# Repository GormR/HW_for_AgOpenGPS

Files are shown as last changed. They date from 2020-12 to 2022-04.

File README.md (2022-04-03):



### What is "AgOpenGPS"?
AgOpenGPS "AOG" is an open-source project initiated by the Canadian [Brian Tischler](https://www.astech.ca/archives/indexofpastwinners/tischler-brian). It started as parallel driving aid and mapping software for Windows(TM) and turned into a full-control system for steering including section and rate control. Today, many peaceful people from all over the world collaborate and contribute to the project. 

The communication part of the software is called AgIO, and AgDiag is the software part showing an overview about all values exchanged between software and hardware. 

On the hardware side, there are several different solutions for the same job, beginning from just plugging readily available module together to the hardware designs provided in this repo for professional prototyping production, which supports all functions of AgOpenGPS in a dedicated design. 

All code is published under the [GNU general public license V3.0](https://www.gnu.org/licenses/gpl-3.0.html) on [Github](https://github.com/farmerbriantee/AgOpenGPS).


All hardware in this repository is published under the [Cern-OpenHardwareLicense-S-2.0](https://cern-ohl.web.cern.ch/).

This text is published under the non-commercial share-alike [Creative Commons License V4](https://creativecommons.org/licenses/by-nc-sa/4.0/deed.en).


All this keeps the project open for everyone in the future. Everyone is allowed to copy and produce everything of this project, but has to open her/his mods for the community in return.

This document describes the system and the hardware. A description of the software itself comes with [the manual embedded in the AgOpenGPS software packet.]([https://github.com/farmerbriantee/AgOpenGPS/releases)

Join the [AgOpenGPS forum](https://discourse.agopengps.com/) for further help and discussions.

>### Important Functional Safety Advice
>
>Agricultural steering systems have to meet at least the agricultural performance level AgrPL d acc. UN ECE R79 (see professional systems like [this](https://www.mobil-elektronik.com/uploads/media/Prospekt_Brochure_ME_Agricultural_Vehicles_ENG.pdf))!
>
>Especially with hydraulic control, the vehicle may likely get uncontrollable on a failure of the valve-controlling electronic which may result in fatal casualties or serious injuries!
>
>For AgOpenGPS, the required safety level may be archieved by the fail-safe absense of power for the valve/motor controlling unit, meaning this function must meet the requirements of AgrPL d.
>
>**Mind, that YOU are reliable for all what you do with this project!**

----
# Basic Block Diagram
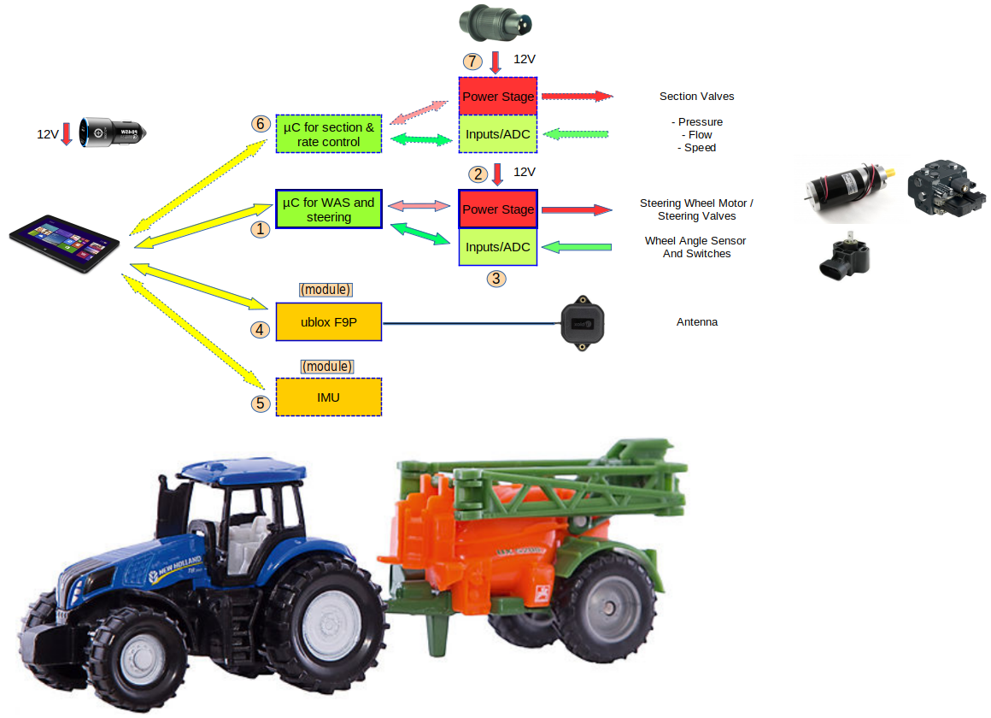
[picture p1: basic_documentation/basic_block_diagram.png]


1. µC e. g. Arduino Nano, Teensy4.1, ESP32,... controlling the power stage and sampling wheel angle sensor (WAS) and optionally IMU data. Also reads the switches 
2. Power stage to drive a motor or hydraulic valves
3. Input section: Analog-digital converter for WAS signal and decoupling for buttons
4. Satellite navigation receiver (GNSS) with RTK precision + antenna (one or two sets)
5. IMU unit
6. Section and rate control (option)
7. Power stage and analog frontend for section and rate control

All blocks but the antennas may be integrated into one PCB - see "Central Units"

# Getting Started, Level 1: Parallel Driving Aid and Mapping

A tablet/notebook/convertable computer running Windows and an RTK-enabled GNSS (GPS) receiver is needed. Read [the posts in the forum](https://discourse.agopengps.com/search?q=which%20tablet) to find a suitable tablet. The screen and its brightness is of highest importance. Other helpful features, you may need, are GSM (mobile data) for the reception of NTRIP data for real-time correction of the GNSS data (instead of using the mobile phone), easy charging for 12V or Ethernet, if USB is not used.

The "standard" RTK GNSS receiver for AgOpenGPS is based on the [ZED-F9P module from ublox](https://www.u-blox.com/en/product/zed-f9p-module), if you don't have an onboard receiver in the tractor. Ready-to-use boards ship from [Ardusimple](https://www.ardusimple.com/product/simplertk2b/) for less than 200€ or $. This is the only option where you can start with a single antenna and migrate to dual-antenna later one. Even two Ardusimple boards are by far less expensive than dual-receivers from [Serpentrio](https://www.septentrio.com) or [Bynav](https://www.bynav.com/). There is no noteworthy difference in precision between these receivers. The Ardusimple board is the de-facto standard for AgOpenGPS. [Here](https://www.optimalsystem.de/os/docs/u-blox-gnss-konfigurationsanleitung.pdf) is a good introduction in German. For details of the technology see [J. M. Olivart i Llop, D. Moreno-Salinas and J. Sánchez: Full Real-Time Positioning and Attitude System Based on GNSS-RTK Technology](https://www.mdpi.com/2071-1050/12/23/9796/htm).

**Parts list**
- tablet/notebook/convertable computer for Windows 7 or higher
- [Ardusimple receiver with antenna](https://www.ardusimple.com/product/simplertk2b-basic-starter-kit-ip65/) or equivalent 
- USB-cable A-microB
- 12V charger for computer (optional but recommended)

**Installation:**
- Download and install [AgOpenGPS software packet]([https://github.com/farmerbriantee/AgOpenGPS/releases)
- Configure the Ardusimple with the help of the software ["ucenter"](https://www.u-blox.com/en/product/u-center) (not version 2!) and [this setup file](central_unit_2.0/code/Ardusimple_GGA_VTG_460.txt)
- connect charger - computer - GNSS-receiver - antenna in a row (the USB receptacle next to the antenna plug is the right one)
- start AgOpenGPS and configure the NTRIP server in AgIO
- put the antenna outside and see, if position data is received (should lock to RTK after a while)
- start mapping with AgOpenGPS

"NTRIP" is the data needed to make cm-precision to GNSS positioning. Precise satellite-based navigation systems do not only a time-of-flight measurement, but also a detecting of the signal phases. Therefore, your position is send to a server every 10 seconds, and you receive customized correction data once per second in return. This only works well, if the server is located quite close to you (<30 km). The availability of public NTRIP serves varies from country to country. There is also the option to run [your own server](https://discourse.agopengps.com/t/rtkbase-a-gui-for-your-own-gnss-base-station/2341/214?u=goronb). 

Generally, the precision is impressive, when considering that light needs 1 second for 300,000km, so it only takes 33 nanoseconds = 0.000000033 sec per centimeter and even the wavelength of the GPS is much higher (about 20 centimeters).

Data sent by the GNSS receiver follows the [NMEA standard](https://en.wikipedia.org/wiki/NMEA_0183). For AgOpenGPS, the number of sentences should be as low as needed, so only "GGA" for position and "VTG" for speed vector.

# Level 2: Steering
There are two possibilities for steering: Turning the wheel like the driver does or driving the hydraulic system directly. Fortunately the electrical part is about the same (two PWM signals) and only the actuator differs: Either a DC motor or a dedicated proportional valve. 
For AgOpenGPS, feedback from a wheel angle sensor "WAS" is always needed, although an incremental sensor at the DC motor would work as well. The best choice is measuring the signal of the build-in WAS, if there is one, but there are also lots of how-tos for adding an additional WAS.

There are 3 different approaches for driving a motor or valves:
- plugging together readily available boards (e. g. Arduino Nano with ADS1115, BNO085 and IBT-2/Cytron - plans are in the AgOpenGPS ZIP file)

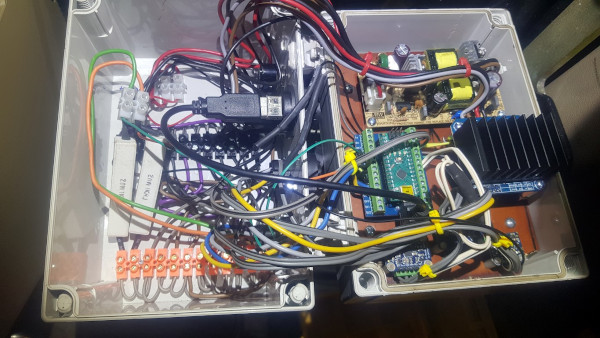
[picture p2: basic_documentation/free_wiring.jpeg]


- using a carrier board for those boards, which adds power supply and necessary components in classic "THT" technology (you have to solder all parts yourself - such boards are discussed in the forum)

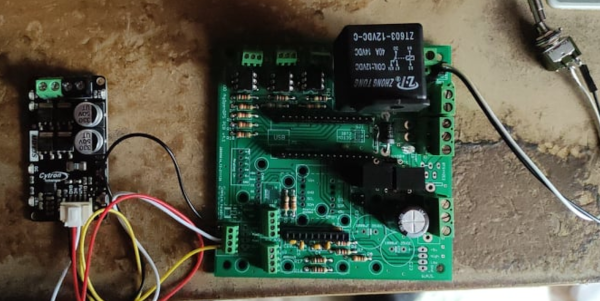
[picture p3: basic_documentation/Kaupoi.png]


- ordering one of the full-equipped board in this repository from a PCB manufacturer (only some "simple" parts have to be soldered by yourself)

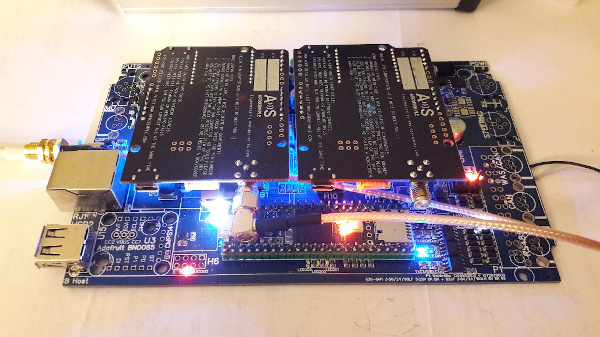
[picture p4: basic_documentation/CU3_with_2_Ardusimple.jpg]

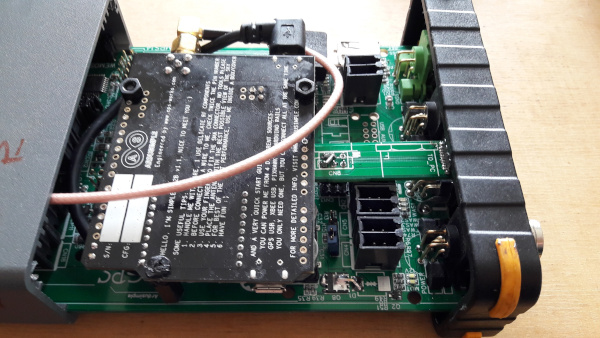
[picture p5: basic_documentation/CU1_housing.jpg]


Honestly, the last option is a nightmare these days, because some key parts (e. g. the automotive PWM power stage drivers) are not in stock from common distributors due to the general shortage in semiconductor industry these days (spring 2022). This means, you have to source from different suppliers and solder some SMD parts yourself, which is not easy in some cases. 

Nevertheless, this option is described in detail now:

**Parts list**
- tablet/notebook/convertable computer for Windows 7 or higher
- [one or two Ardusimple receiver with antenna](https://www.ardusimple.com/product/simplertk2b-basic-starter-kit-ip65/) or equivalent 
- IMU unit based on BNO08x
- mainboard + housing
- cables
- 12V charger for computer (the Central Unit 3.0 has a build-in charger, but no software support yet)
- steering wheel motor or hydraulic unit + support material

**Installation:**
- Download and install [AgOpenGPS software packet]([https://github.com/farmerbriantee/AgOpenGPS/releases)
- Configure the Ardusimple with the help of the software ["ucenter"](https://www.u-blox.com/en/product/u-center) (not version 2!) and [this setup file](central_unit_2.0/code/Ardusimple_GGA_VTG_460.txt)
- assemble board and put it into the housing
- prepare cables 
- connect everything
- start AgOpenGPS and configure the NTRIP server in AgIO
- put the antenna outside and see, if position data is received (should lock to RTK after a while)
- start working with AgOpenGPS

# Hints for Wiring
All signals to the motor or hydraulic valve shall be inside a single cable. This cable may only be connected to the Central Unit and the motor/valve unit - nowhere else. So no connection between the valve unit and the chassis as long as you don't want to use your equipment for short-wave broadcasting!

WAS:
If there is a dedicated WAS for AgOpenGPS, use a 3-pole calbe running from the Central Unit to the WAS. It contains the signals +5V, "WAS" = analog output of the WAS and 0V = GND. No other connections like "grounding" somewere in this case either! If a factory-assembled WAS shall be "sourced" like in the following pictures, a two-pole cable with the signals "WAS" (again the analog output of the WAS) and "WAS_N" is needed. Mind that the cable number differs! Connect "WAS_N" to 0V next to the point where you already connected the "WAS". 

The original wire was not cut but the isolation was just partially cut from one side. Advantage here: It's inside the cabin and always dry.

With one of the central units, select "differential" in AgOpenGPS in both cases.

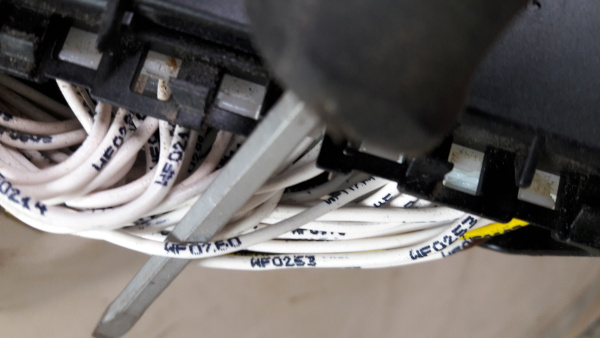
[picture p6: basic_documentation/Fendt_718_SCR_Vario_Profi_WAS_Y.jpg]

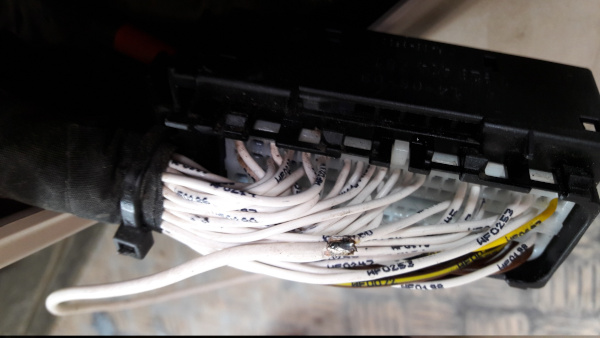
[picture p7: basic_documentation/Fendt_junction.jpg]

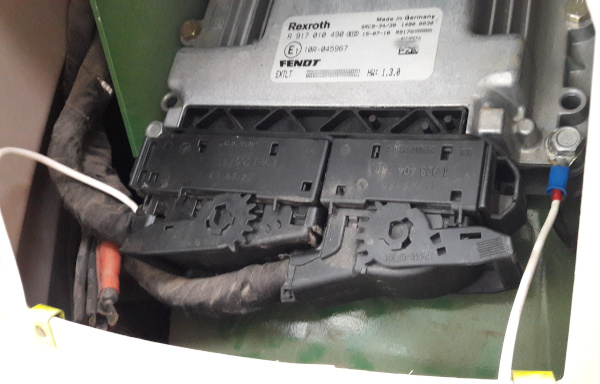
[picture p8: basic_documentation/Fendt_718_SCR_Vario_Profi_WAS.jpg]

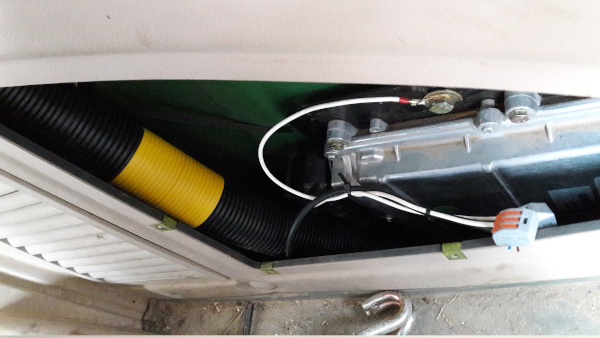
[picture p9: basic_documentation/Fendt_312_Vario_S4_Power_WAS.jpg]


There is intentionally no coupling of 0V from power stage and computer side on the Central Unit 1.x and 2.x, because the charger unit has that normally. If this is not the case (e. g. you're using an inverter and a charger with mains plug), the connection must be done manually.

# Dual-GNSS? IMU? Both?
When you living in a plain area with no hills, you can start farming now. But likely there are rolling hills around and your fields are sloping a little bit, so that the antenna position swings left and right with the slope of the field and there is a need to compensate that by either using two antennas with two RTK receivers or and an	inertial measurement unit (IMU). 

Pros of dual antenna are:
- always absolute position in the room
- antenna diversity: if one antenna does not receive the signal due to trees, the other one will take over for that time

Pros of IMU:
- Cheaper
- Roll angle is more exact
- Reduced update rate if using two Ardusimple with cross-communication (8Hz instead of 10Hz). Solution: Connect both F9P directly to the PC via USB (same setup file).
 
The z axis of the IMU must be exactly the vertical axis of the vehicle. Recommended is the use of an BNO085 or BNO080 - directly or embedded in the CMPS14 board.

# Arduino-Nano or Teensy-based?
For all 3 different approaches, these two options are available (plus ESP32 to name the third). The Teensy has more memory and is faster - both more than 100 times). The advantage today is: simply nothing, as long as you don't use CAN or main parts of AgOpenGPS run inside the iMX controller. Maybe in future, AgOpenGPS will migrate there and has just have a web page on any mobile device. This would also improve the steering behaviour noteworthy due to reduced jitter times (no Windows in between).

# IBT-2 or Cytron
First of all: None of them for driving a Danfoss block - a rail-to-rail operational amplifier will do that job as well.

Intergrated boards will always use what the IBT-2 is using, because there is no need to care for short-circuits due to miswiring or mechanical damage. The drivers have a build-in protected agains all that. And there is no need for a freewheeling relay if a steering wheel motor is used. 

When using complete boards, further arguments matter: Yes, the IBT-2 is cheaper, but there are a lot of bad-quality boards out in the wildlife. Control the solderings and always add a thermal pad between the board and the heat sink! The solder mask is no suitable isolation between the PCB and the heat sink! These qualitiy problems are avoided by buying the Cytron. But the Cytron blocks manual steering, when AgOpenGPS isn't in control, because it short the motor wires - it acts as electrical brake, which is not intended in this use-case. Any kind of disengagement is needed.

# USB or Ethernet
Many discussions have been made about the "right" interface between the computer and the peripherals. In fact: Both kind of connectors, USB and Ethernet, are not suitable for agricultural use. Professional systems use M8 and M12 connectors. The type "M12-D" is well-suitable for both Ethernet and USB, but no computer has such a connector... An option is soldering yourself, but another option is just having some spare cables in the box. 

An important point is the ability to transport supply power. For Ethernet, that makes some effort and only a few devices support PoE. USB always have that feature, so you can use just one USB-C cable for charging the computer and transfer data to the peripherals. Clear point of USB, as long as two-wire Ethernet is not commonly available for adequate costs.

My suggestion: If you ever dreamt of being a professional network admin, go for Ethernet. All others should use USB. Here, the Teensy may bring both worlds together by using RNDIS (Ethernet over USB) one day.

**Timing**

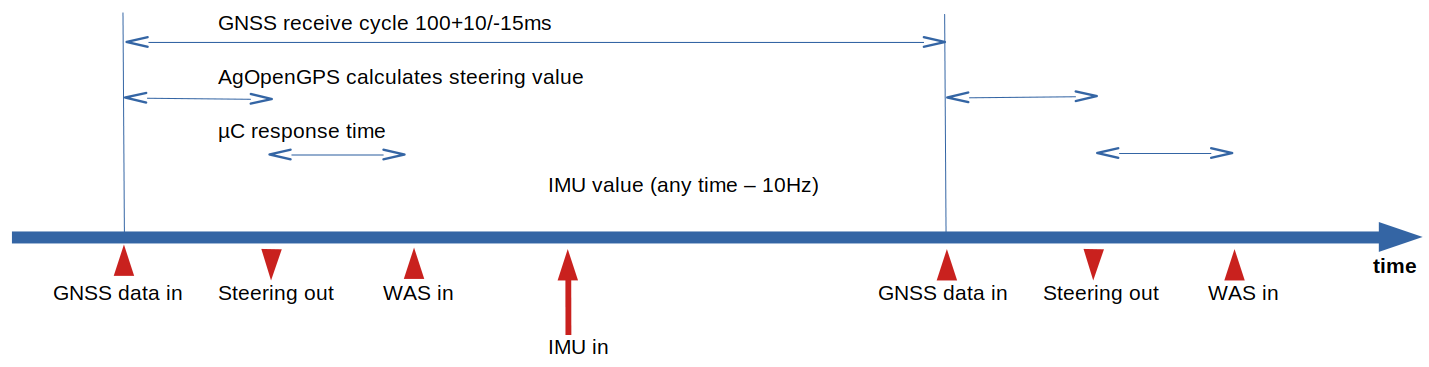
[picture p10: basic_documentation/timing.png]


This is the basic timing of AgOpenGPS. It is defined by the GNSS update cycle, so about 100ms for the F9P (Ardusimple) board. The postion data is an average of the last period, so the position is about 50ms "old". After having received that data, AgOpenGPS calulates all the steering data and sends it to the µC unit, that delivers the position of the steering (from wheel angle sensor) and optionally the IMU data in return. This is obviously not the best time, because that data is about 90ms old when processed by AgOpenGPS.

Using an extra µC for the IMU ("IMU_USB_v5_0.ino") even makes the timing even worse, because data receives at *any* time, so we don't have a delay but a fully unpredictable jitter. One workaround will come the AgOpenGPS V6 - there will be a unit that combines GNSS and IMU data into one non-standard NMEA sentence.

The best timing is archieved with no additional µC at all for GNSS and IMU. Both units are able to send serial data directly to the PC. All you need for the GNSS receivers is a USB cable and an USB-serial-converter cable for the IMU. The jitter simply can't be less.

Connection [of USB-Serial-Cable](https://de.aliexpress.com/item/32965292523.html) to BNO085 in RVC mode: 1st pic shows USB cable supplying board with 5V, if there is a voltage regulator on it; 2nd pic shows the same cable w/o using the voltage regulator. The 1st is prefered for this Adafruit board, the 2nd is for all boards w/o voltage regulator like shown in the 3rd picture. Supply voltage is about 3.05V in that case :+1:

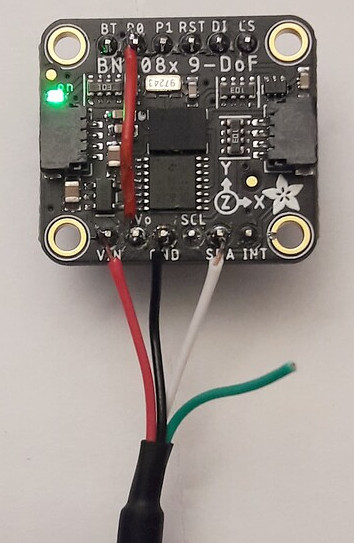
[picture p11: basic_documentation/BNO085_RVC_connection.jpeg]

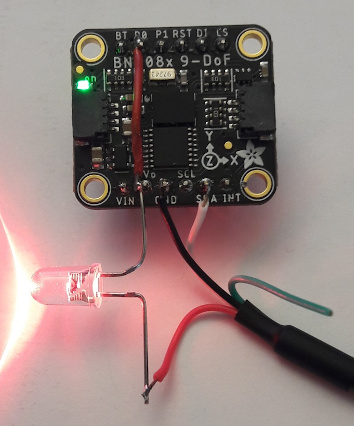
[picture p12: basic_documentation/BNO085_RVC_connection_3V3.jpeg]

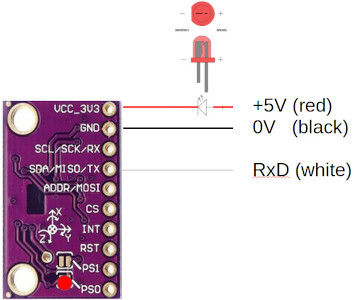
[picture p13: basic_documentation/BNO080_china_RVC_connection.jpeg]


For those who prefer Ethernet connections: This is how to connect two Ardusimple to AgIO via an Ethernet cable. [This module can connect two serial devices](https://www.pusr.com/products/dual-UART-to-ethernet-module-usr-tcp232-e2.html), in this case two [Ardusimples @ 460800Bd](https://github.com/GormR/HW_for_AgOpenGPS/tree/main/central_unit_2.0/code) to Windows. 

Will also work for one Ardusimple and one BNO085 in RVC mode.

The red wire is the +5V supply - FIVE volt supply.

black: 0V
red: 5V
brown: 3.3V
green: to Ardusimple (NTRIP; RxD@AS, TxD@USR)
white: from Ardusimple (NMEA data; TxD@AS, RxD@USR)

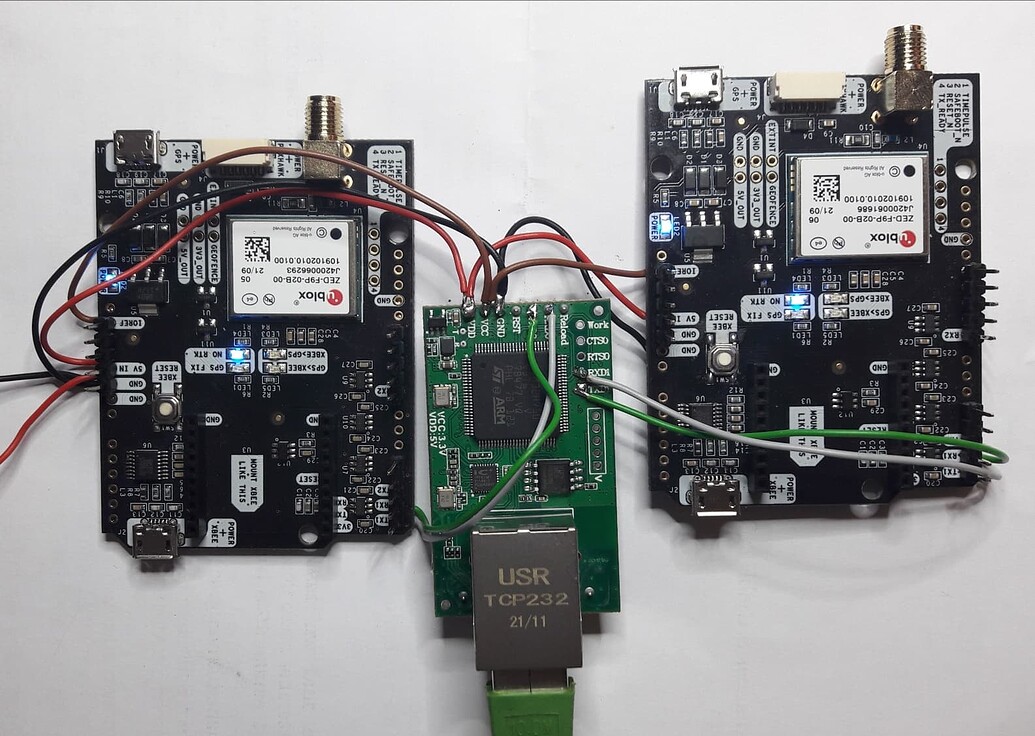
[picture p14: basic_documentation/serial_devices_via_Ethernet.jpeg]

(same colors used as above for the BNO085)

The connection to the Ardusimple board can also be made by [the plugable Pixhawk connectors using 0V, 5V and the two communication lines.](https://www.ardusimple.com/simplertk2b-hookup-guide/) In that case, connecting the 3.3V line is not needed, but I would put a 100 Ohms resistor in series with the com lines.

The BNO085 is difficult to buy these days, so it’s worth having a look at the Arduino Nano RP2040 Connect board with its integrated IMU. A prototype implementation using this one for AgOpenGPS can be found in [this Github repo](https://github.com/GormR/HW_for_AgOpenGPS/central_unit_2.0/code/Arduino_nano_connect_as_IMU/). The IMU itself is as good the the Bosch sensor of the BNO, but there is no magnetic sensor and so a continuous calibration of the heading isn’t possible so far. A certain drift is remaining, but may be eliminated in combination with AgIO one day.

With the Python script, the sensor emulated an BNO085 in RVC mode being compatible with the AgIO mod. [Here](central_unit_2.0/code/) is the replacement for the standard AgIO.exe. Just replace it by this file and work with the data of the BNO or Arduino Connect directly.

----
# Projects within the repository

All projects use a robust housing and industrial M12/M8 connetors (optional) as far as possible. There is also an option to use industrial PushIn connectors instead.

The PCB project was set up with the EDA program „EasyEDA“, which is freely usable. 

*These products are still working perfectly with AgOpenGPS, but not recommended for new systems*

[Documentation Central Unit](central_unit/README.md)

[Documentation Rooftop Unit](rooftop_unit/README.md)

[Documentation Ethernet Adapter for UDP](ethernet_adapter/README.md)

**Latest Main boards**

Update of Central Unit 1.x with 2nd slot for dual-Ardusimple:
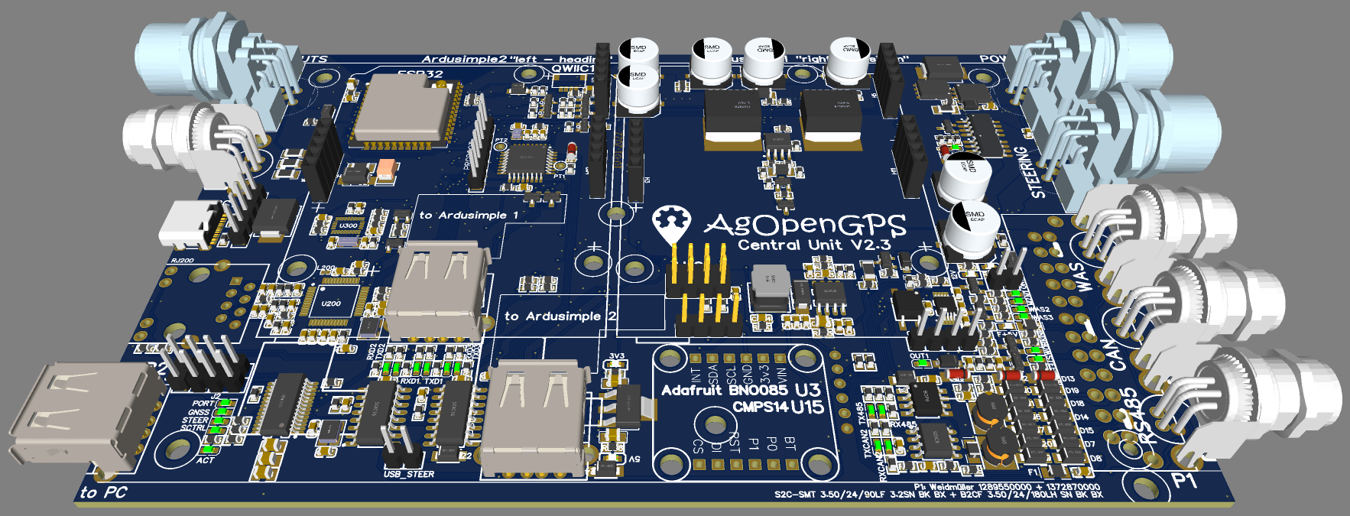
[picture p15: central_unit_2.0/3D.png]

[Documentation Central Unit 2.x](central_unit_2.0/README.md)

There is a [reduced BOM](central_unit_2.0/production_data/BOM_CentralUnit2.3_(USB-recommended).csv) for USB (estimated board price @ JLCPCB: $30 after the semiconductor prices will have returned to normal levels again).

Teensy-based central unit with additonal support for USB-PD hardware (no firmware support yet):
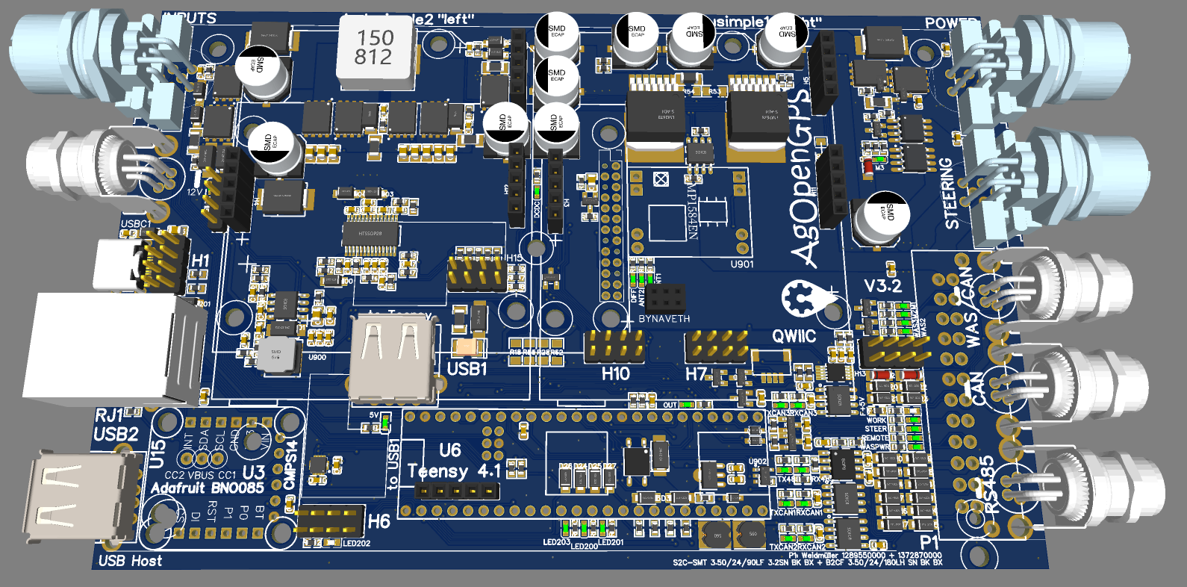
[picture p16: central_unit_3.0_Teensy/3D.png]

[Documentation Central Unit 3.x](central_unit_3.0_Teensy/README.md)

(This board also has a slot for Bynav-GNSS-receivers)

# Order How-To JLCPCB
- browse to [JLCPCB](https://jlcpcb.com) and click "Quote now"
- upload Gerber file (either for [Centrol unit](central_unit/production_data/Gerber_Central_Unit_AgOpenGPS.zip) or [Rooftop Unit](rooftop_unit/production_data/Gerber_Rooftop_Unit_AgOpenGPS.zip)). The Gerber of the central unit is too big for a preview, so you also have to enter the DIMENSIONS in the next line after the upload process has fully finished: 150 x 92mm²
- enter the number of PCBs to order: 5, 10, 15, etc
- if you like, you may change the color of the solder mask printing. But not all colors are available for SMD manufacturing!
- for the central unit check switch "SMT assembly" and "Assemble top layer"
- Accept terms and click "NEXT" (you may log in now)
- Upload [BOM](central_unit/production_data/BOM_Central%20Unit%20for%20AgOpenGPS.csv) and [Pick and Place file](central_unit/production_data/PickAndPlace_Central_Unit_AgOpenGPS.csv)
- click NEXT
- browse through the list and see, what is not confirmed. For some you may find 2nd sources, some maybe not available from stock in that moment, some like the Nexperia controller are unavailable and some like connectors are not supported yet (see my [video](https://www.youtube.com/watch?v=dLczChhmDCY) how to solder the USB-C receptacle; soldering the USB-C receptacle like this is only necessary, if you want to use a single USB cable for charging and data. USB itself is also connectable via a dedicated PushIn connector)
- click NEXT
- check if all components are placed correctly (e. g. rotation information is sometimes incorrect in the libraries)
- order

# (German copy)



### Was ist "AgOpenGPS"?
AgOpenGPS "AOG" ist ein open-source-Project, das vom kandischen Farmer [Brian Tischler](https://www.astech.ca/archives/indexofpastwinners/tischler-brian) initiiert wurde. Es war zunächst eine reine Parallelfahrhilfe und wurde nach und nach mit Hilfe der Community zu einem Lenksystem mit Teilbreitensteuerung. Die Software läuft nur unter Windows(TM) - es wird also ein Windows-Tablet oder Notebook benötigt. Inzwischen arbeiten Interessierte aus aller Welt friedlich an der Weiterentwicklung des Projektes. 

Die Software ist ein Set aus drei Programmen: Der Kommunikationsteil heißt AgIO, und AgDiag ist eine Anzeige aller Zustände und ausgetauschten Daten. 

Hardwareseitig gibt es vielfältige Ansätze für dieselbe Aufgabe. Das reicht von Anleitungen, wie man Arduino-Module mit Sensor- und Aktorboards zusammensteckt über Trägerplatinen, auf die man diese Module auflötet bis hin zu den in diesem Repository hinterlegten Modulen, die man als Fertigplatine bei einen Leiterplattenbestücker in Auftrag geben kann und die alle Funktionen von AgOpenGPS in einer Einheit unterstützen.

Die gesamte Software ist unter der  [GNU general public license V3.0](https://www.gnu.org/licenses/gpl-3.0.html) auf [Github](https://github.com/farmerbriantee/AgOpenGPS) veröffentlicht.


Alle Hardwareprojekte in diesem Repository sind unter der [Cern-OpenHardwareLicense-S-2.0](https://cern-ohl.web.cern.ch/) veröffentlicht.

Diese Beschreibung steht unter der nichtkommerziellen [Creative Commons License V4](https://creativecommons.org/licenses/by-nc-sa/4.0/deed.de).


Dadurch wird sichergestellt, dass das Projekt jetzt und in Zukunft allen zugänglich ist und alle Weiterentwicklungen der Community wieder zu Gute kommen.

Dieses Dokument beschreibt das System und die Hardsware. Eine Softwarebeschreibung befindet sich in einem [PDF, das sich im ZIP zusammen mit der Software befindet.]([https://github.com/farmerbriantee/AgOpenGPS/releases)

Es gibt ein (englisches) [AgOpenGPS forum](https://discourse.agopengps.com/), wo viele Leute unterschiedlichste Anwendungsfälle diskutieren.

>### Wichtiger Hinweis zur Funktionalen Sicherheit
>
>Fest verbaute Lenksystem, die z. B. in die Hydraulik eingreifen, müssen den Agricultural performance level AgrPL d nach UN ECE R79 (siehe z. B. professionelle Systeme wie [dieses](https://www.mobil-elektronik.com/uploads/media/Prospekt_Brochure_ME_Agrarfahrzeuge_DEU.pdf)) erfüllen!
>
>Im Falle eines Ausfalls und dadurch ausgelösten Lenkbewegungen kann es zu tödlichen Unfällen oder schweren Verletzungen kommen!
>
>Mit AgOpenGPS kann der notwendige Sicherheitslevel durch die fehlersichere Abschaltung der elektrischen Leistung für die Lenkaktoren erfolgen. Diese Abschaltung muss mindestens diesen Sicherheitslevel erfüllen.
>
>Alle Daten diese Repositories stehen unter der CERN Open-Hardware-Lizenz 2.0. Jede Haftung für Personenschäden und Sachschäden auf Grund Fehlern der Beschreibung oder Fehlern der Leiterplatte oder Software wird ausgeschlossen! 
>
>**Du bist dafür verantwortlich, was du mit diesem Projekt machst!**

----
# Grundlegendes Blockdiagram


1. µC, also z. B. Arduino Nano, Teensy4.1, ESP32,... steuert die Leistungsendstufe und liest die Werte des Lenkwinkelsensors (LWS = WAS), der Schalter nd ggf. der IMU ein
2. Leistungsendstufe, um den Motor oder die Hydraulik zu bedienen
3. Eingänge: Analog-digital-Wandler für das LWS-Signal und Eingangsstufe für die Schalter
4. GPS-Empfänger (GNSS) mit RTK-Genauigkeit + Antenna (ein oder zwei Paare)
5. IMU-Einheit
6. Teilbreiten- und Volumensteuerung (optional)
7. Leistungsendstufe und Analogteil der Teilbreiten- und Volumensteuerung

Alle Blöcke bis auf die Antennen können sich in einem Gehäuse befinden, z. B. auf den Leiterplatten in diesem Repository

# Getting Started, Level 1: Parallelfahrhilfe und Dokumentation

Für den Einstieg wird ein Tablet, Notebook oder Convertable mit dem Betriebssytem Windows une ein RTK-fähiger GNSS-(GPS)-Empfänger benötigt. Eine Beratung zum Rechner gibt es [in diesen Posts im Forum](https://discourse.agopengps.com/search?q=which%20tablet). Das ist natürlich immer nur eine Momentaufnahme. Wichtig ist in jedem Fall eine hohe Bildschirmhelligkeit. Weitere wichtige Punkte sind neben der Gesamtperformance die Möglichkeit, mobile Daten zu empfangen (eingebautes GSM-Modem), falls kein Handy dafür verwendet werden soll, um die NTRIP-Daten für die Positionskorrektur zu empfangen, eine einfache Lademöglichkeit für 12V und Ethernet, falls man USB nicht verwenden möchte.

Die Mehrzahl der RTK-GNSS-Empfänger für AgOpenGPS basieren auf einem [ZED-F9P-Module von ublox](https://www.u-blox.com/en/product/zed-f9p-module), aber auch bereits vorhandene Systeme der Traktorhersteller können verwendet werden. Fertige Empfängerplatinen gibt es z. B. bei [Ardusimple](https://www.ardusimple.com/product/simplertk2b/) für weniger als 200€. Das ist auch die einzige Möglichkeit, zunächst mit einem Ein-Antennen-System zu starten und später auf zwei Antennen aufzurüsten. Dabei sind zwei Ardusimples + zwei Antennen immer noch deutlich günstiger als Dual-Receiver von  [Serpentrio](https://www.septentrio.com) oder [Bynav](https://www.bynav.com/). Nennenswerte Genauigkeitsunterschiede haben die Systeme nicht. Das  Ardusimple-Board ist deshalb nicht umsonst der de-facto-Standard bei AgOpenGPS. 

[Hier](https://www.optimalsystem.de/os/docs/u-blox-gnss-konfigurationsanleitung.pdf) gibt es eine guten Anleitung zur Konfiguration. Grundlagen zur RTK-Technologie finden sich in [J. M. Olivart i Llop, D. Moreno-Salinas and J. Sánchez: Full Real-Time Positioning and Attitude System Based on GNSS-RTK Technology](https://www.mdpi.com/2071-1050/12/23/9796/htm) ein englischer Sprache.

**Einkaufsliste**
- Tablet/Notebook/Convertable-Computer mit Windows 7 oder höher
- [Ardusimple-Empfänger mit Antenne](https://www.ardusimple.com/product/simplertk2b-basic-starter-kit-ip65/) oder vergleichbarer Empfänger 
- USB-Kable A-microB
- 12V-Ladegerät für den Computer (optional aber empfehlenswert)

**Installation:**
- [AgOpenGPS software packet]([https://github.com/farmerbriantee/AgOpenGPS/releases) downloaden und installieren 
- Ardusimple konfigurieren mit der Software ["ucenter"](https://www.u-blox.com/en/product/u-center) (nicht die Version 2 benutzen!) und [diesen Setup-Daten](central_unit_2.0/code/Ardusimple_GGA_VTG_460.txt)
- Ladegerät, Computer - GNSS-Empfänger und Antenne einer einer Reihe verbinden (die USB-Buchse neben dem Antennenstecker ist die richtige)
- AgOpenGPS starten und den NTRIP-Server in AgIO konfigurieren (in D sollten im Allgemeinen die Daten von Sapos verwendet werden)
- Antenne nach draußen stellen und warten, bis Positionsdaten angezeigt werden. Nach einer Zeit sollte auch "RKT" angezeigt werden.
- Aufs Feld fahren und loslegen

Mit "NTRIP" werden Korrekturdaten bezeichnet, die benötigt werden, um eine Genauigkeit im cm-Bereicht zu erreichen. Dazu muss der Empfänger nicht nur die Signallaufzeit zwischen den Satelliten und der Antenne messen, sondern auch die Phase des Empfangssignals. Die notwendigen Korrekturdaten liefert ein NTRIP-Server, der über eine Referenzantenne verfügt, dessen Position hochgenau bekannt ist und sich in der Nähe befinden muss (< 30km). Man kann einen solchen Server auch [selbst](https://discourse.agopengps.com/t/rtkbase-a-gui-for-your-own-gnss-base-station/2341/214?u=goronb) betreiben, allerdings gibt es im deutschsprachigen Raum kostengünstige, professionelle Angebote wie z. B. SAPOS speziell for Landwirtschaft und Vermessung.

Folgende Daten werden für SAPOS benötigt:
- Server-IP (hier am Beispiel Nordrhein-Westfalen: www.sapos-nw-ntrip.de (AgIO kann damit automatisch die IP (hier: 80.158.61.104) und den Port (hier: 2101) ermitteln
- Benutzerkennung in der Form "nw-123456"
- Passwort in der Form "abcdef"

Insgesamt ist die erreichbare Genauigkeit beeindruckend, wenn man bedenkt, dass Licht und damit auch Funkwellen 300.000km in einer Sekunde zurücklegen, man also nur 33 Nanosekunden für einen cm benötigt und selbst die Wellenlänge der Trägerfrequenz mit ungefähr 20cm deutlich größer ist.

Ein GNSS-Empfänger sendet die Daten im [NMEA-Format](https://de.wikipedia.org/wiki/NMEA_0183). Die Einstellungen sollten so sein, dass möglichst nur die notwendigen Sätze "GGA" für Position und "VTG" für den Geschwindigkeitsvektor gesendet werden (s. u.).

# Level 2: Automatische Steuerung
Es gibt zwei grundsätzlich verschiedene Möglichkeiten der Steuerung: Direkt über Hydraulikventile oder mit Hilfe eines Elektromotors am Lenkrad drehen. Einen Eingriff in die Hydraulik sollten nur diejenigen vornehmen, die wirklich verstanden haben, was AgPL d bedeutet und es umsetzen können. Auch wenn es natürlich das eleganteste ist... Zu unterscheiden sind hier Systeme, die aus zwei Ventilgruppen bestehen (Steuerventil und Umschaltventil zwischen Lenkrad und AgOpenGPS-Steuerventil) und "intelligenten" Ventilinseln, wie z. B. "Danfoss".

Bei Lenkradmotoren hat sich der Phidgets-Motor als meistverwendeter herausgestellt, obwohl natürlich auch vergleichbare Motoren funktionieren. Zu unterscheiden sind Ankopplungen über ein Reibrad und Zahnradlösungen, bei denen das Ritzel des Motors in ein Zahnrad eingreift, das am Lenkrad festgeschraubt ist. Beide Lösungen haben sicherlich ihre Vorteile - wichtig ist, dass der Fahrer jederzeit ins Lenkgeschehen eingreifen kann! 

Motor oder Hydraulik: Zum Glück sind die Ansteuersignale dieselben: 2 PWM-Leistungssignale. Für das Umschaltventil muss bei Hydraulik zusätzlich noch ein Enable-Signal entsprechender Leistung bereitgestellt werden. "Danfoss"-Ventile können ebenfalls über 2 PWM angesteuert werden, es reicht allerdings ein einfacher Operationsverstärker als "Leistungsendstufe".

AgOpenGPS benötigt immer einen Lenkwinkelsensor, obwohl technisch auch eine Regelung über einen Tachogeber am Motor möglich wäre. Aber zum Glück haben ja viele Traktoren bereits eingebaute Sensoren, und es gibt auch sehr gute Anleitungen, einen Sensor einzubauen.

Für die Steuerung gibt es nun drei verschiedene Ansätze:
- man kauft sich fertige Teilmodule (Arduino Nano, ADS1115, ...) und verdrahtet diese "fliegend" in einem geeigneten Gehäuse



- man lässt sich eine fertige Leiterplatte herstellen, die für ein paar Euro aus China angeflogen kommt. Die Bestückung mit "klassischen" THT-Bauteilen muss man dann selber durchführen und auch die o. g. Teilmodule hier wieder auflöten



- man bestellt sich eine der vollständig bestückten Leiterplatten aus diesem Repository. Dann müssen nur noch die gewünschten Stecker angelötet werden.




In jedem Fall muss natürlich die Software auf den µC aufgespielt werden. Eine Beschreibung dazu befindet sich bei den einzelnen Leiterplatten.

Aus aktuellem Anlass muss aber leider gesagt werden, dass die letztgenannte Möglichkeit aktuell (Frühjahr 2022) sehr mühselig ist, da Schlüsselbauteile wie µC und Leistungstreiber nicht ab Lager verfügbar sind und somit anderweitig beschafft und selbst aufgelötet werden müssen. Leider kein Spaß für viele und erst einmal keine Besserung in Sicht.

**Einkaufsliste**
- Tablet/Notebook/Convertable-Computer für Windows 7 oder höher
- [ein oder zwei Ardusimple-Empfänger mit Antenne](https://www.ardusimple.com/product/simplertk2b-basic-starter-kit-ip65/) oder vergleichbarer Empfänger
- IMU auf Basis eines BNO080 oder BNO085 (auch als CMPS14-Board möglich)
- eines der Mainboard aus dem Repository hier + Gehäuse
- Kabel
- ein 12V-Ladegerät für den Computer (die Central Unit 3.0 hat ein eingebautes USB-C-PD Ladegerät, aber bisher keinen passenden Treiber)
- Lenkradmotor oder Hydraulikeinheit und Zubehör dafür

**Installation:**
- [AgOpenGPS software packet]([https://github.com/farmerbriantee/AgOpenGPS/releases) downloaden und installieren
- Ardusimple konfigurieren mit der Software ["ucenter"](https://www.u-blox.com/en/product/u-center) (nicht die Version 2 benutzen!) und [diesen Setup-Daten](central_unit_2.0/code/Ardusimple_GGA_VTG_460.txt)
- Mainboard mit Steckern bestücken und programmieren; Ardusimple-Boards aufstecken, wenn sie mit im Gehäuse sein sollen
- Kabel vorbereiten
- Alles verbinden
- AgOpenGPS starten und den NTRIP-Server in AgIO konfigurieren mit den eigenen Zugangsdaten (Sapos z. B.)
- Antenne im Freien aufstellen. Nach einer Zeit sollte der eigene Standort angezeigt werden und auch die Anzeige "RTK" erscheinen
- Los auf's Feld und AgOpenGPS ausprobieren

# Dual-GNSS? IMU? Oder beides?
Landwirte in im nördwestlichen Niedersachsen können jetzt loslegen. Alle anderen haben wahrscheinlich das ein oder andere Feld in Hanglage, und da läuft dann die eigene Position mit der Hangneigung weg, weil der Fußpunkt der Antenne zur Seite wandert. Also muss das kompensiert werden, wozu es eben diese beiden Möglichkeiten gibt: Eine zweite RTK-Empfänger/Antennenkombination oder eine IMU (inertial measurement unit - Inertiale Messeinheit, also ein Sensor, der die relative Lage im Raum an Hand der Schwerkraft und Massenträgheit bestimmen kann).

Vorteile Dual-GNSS:
- hat immer die absolute Position im Raum
- "Antenna-Diversity": Der kurzzeitige Ausfall einer Antenne führt nicht zum Verlust der Genauigkeit, z. B. wenn eine Seite von einem Baum abgeschattet wird

Vorteile IMU:
- Kostengünstiger
- Genauere Winkelerfassung
- Wenn zwei Ardusimple mit Querkommunikation betrieben werden (z. B. an einem ESP32), verringert sich die Datenrate der Position von 10 auf 8 pro Sekunde. Das kann aber umgangen werden, indem beide Boards direkt über USB mit dem PC verbunden werden (sie haben dann auch das gleiche Setup-File (s. o.).
 
Die z-Achse der IMU muss vertikal montiert sein. Es sollten BNO085 or BNO080-basierte Sensoren verwendet werden - allein oder als CMPS14-Board.

# Hinweise zur Verkabelung
Alle Signale, die zum Motor oder zur Ventilinsel führen, sollten in einem Kabel enthalten sein. Das Kabel darf nur an der Central Unit und am Motor oder an der Ventilinsel angeschlossen sein, sonst nirgendwo, also auch nicht die 0V an der Ventilinsel mit der Karosserie verbinden! Man baut sich so ganz schnell eine Rahmenantenne für Mittelwelle...

LWS/WAS:
Soll ein Extra-Lenkwinkelsensor verwendet werden, sollte ein 3pol. Kabel von der Central Unit zum Sensor verlegt werden, das die Signale +5V, "WAS" = Analogwert des LWS und 0V = GND enthält. Auch hier sollte nichts anderes angeschlossen sein, als der LWS, also auch wieder eine "Erdung" zur Karrosserie oder so. Wenn ein bereits verbauter LWS "angezapft" werden soll wie in den folgenden Bildern gezeigt, muss die Verdrahtung über ein zweipoliges Kabel "differenziell" erfolgen: "WAS" ist wieder der Analogwert des LWS, und "WAS_N" wird an einen 0V-Punkt in der Nähe des Punktes angeschlossen, wo auch "WAS" angeklemmt ist. Achtung: Die Klemmennummer variiert von Modell zu Modell - zumindestens bei Fendt. 

Im Bild wurde der Originaldraht nicht durchgeschnitten, sondern die Isolierung nur seitlich weggeschnitten, um den Draht für AgOpenGPS dann dort anzulöten. Zugentlastung nicht vergessen. Vorteil dieser Lösung: Es liegt alles im Trockenen in der Kabine.

Bei Verwendung der Central Units sollte in beiden Fällen in AgOpenGPS "differenziell" ausgewählt werden.






Bei der Central Unit 1.x und 2.x gibt es ganz bewusst keine harte Kopplung von 0V/GND der Leistungsendstufe und 0V/GND des USB, weil dies normalerweise über das 12V-Ladegerät erfolgt und eine Masseschleife vermieden werden soll. Sollte dies Verbindung nicht vorhanden sein, weil z. B. ein 230V-Netzteil an einem Wechselrichter betrieben wird, muss diese Verbindung manuell hergestellt werden.

# Arduino-Nano oder Teensy?
Für alle drei Möglichkeiten (Module zusammenlöten, auf Trägerplatine löten oder integriertes Board) gibt es zwei zur Auswahl stehende µC: der "klassische" Arduion-Nano-Controller ATMEGA368 oder das Teensy4.1-Board mit iMX1061-Controller von NXP. Der ESP32 und andere mal außen vor - sie haben ihre Daseinsbereichtigung z. B. für WLAN-Lösungen. Der Teensy ist mehr als 100x schneller, hat mehr als 100x mehr Speicher und hat somit - nein, bisher leider garkeinen Vorteil, solange AgOpenGPS weder CAN unterstützt oder wesentliche Softwareteile wirklich im iMX laufen und eine mobile Webside bereitstellen. Wäre super, weil sicherlich auch die Lenkqualität besser würde, ist aber noch Zukunftsmusik.

# IBT-2 oder Cytron
Vorweg: Für Danfoss reicht ein einfacher Operationsverstärker. Für alles andere muss schwereres Geschütz aufgefahren werden.

Die intergraten Board in diesem Repository werden immer die robusten, speziell für die Automobilindustrie entwickelten Infineon-Treiber verwenden, die auch auf dem IBT-2 verbaut sind, weil diese einfach vollständig gegen alle möglichen Fehler und Überlastung vollständig geschützt sind. Außerdem benötigt man nicht unbedingt einen Freilauf für das Lenkrad, weil der Motor nicht nennenswert elektromotorisch gebremst wird.

Wenn man eine Baugruppe fertig zukaufen möchte, kommen noch andere Argumente ins Spiel: Ja, ein IBT-2 ist günstiger, aber zumindeste die billigen China-Clones sind oft von wirklich lausiger Qualität. Hier muss man sich auf jeden Fall die Arbeit machen und den Kühlkörper abschrauben und mit Wärmeleitpaste oder besser einem Wärmeleitpad gegen die Leiterplatte isolieren. Der Lötstopplack alleine ist dafür vollkommen ungeeignet. Das hat zu einem schlechten Ruf dieser Lösung begetragen, ist aber - wie gesagt - auch leicht zu beheben.

Kauft man ein Cytron-Board, bekommt man immer gleich gute Qualität. Allerdings schließt ein Cytron die Motorwicklungen kurz, wenn AgOpenGPS nicht steuert. Dadurch ist es nicht mehr möglich das Lenkrad vernünftig leicht zu drehen. Ein Freilauf wird also auf jeden Fall benötigt.

# USB oder Ethernet
Unzählige Diskussionen gibt es, welches die beste Schnittstelle zwischen AgOpenGPS und der Hardware ist. Die ehrliche Antwort ist zunächst einmal: Sowohl USB als auch Ethernet haben für automobile/landwirtschaftliche Verwendung ungeeignete Stecker. Beide lassen sich allerdings mit den in professionellen Geräten verwendeten M12-D-Stecker versehen und sind dann sogar wasserfest bis IP67. Computer mit einem solchen Stecker sucht man allerdings vergeblich. Selbstlöten ist natürlich möglich oder nimmt Kabel von der Stange und legt sich ein paar als Ersatz ins Handschuhfach.

Ein wichtiger Punkt ist, dass der Anschluss auch den Versorgungsstrom liefern kann. Klarer Vorteil für USB - hier kann sogar der Computer während der Fahrt aufgeladen werden (Treiber vorausgesetzt - siehe oben). Der Vorteil mag sich zukünftig relativieren, wenn automobiles Zweidraht-Ethernet üblicher wird (Single-Pair Ethernet) und ICs zu vertretbaren Kosten für die AgOpenGPS-Gemeinde verfügbar werden.

Meine Meinung: Wer immer schon ein professioneller Netzwerk-Admin werden wollte, nimmt Ethernet. Alle anderen sind mit USB weit besser bedient, zumal man über USB auch das Netzwerkprotokoll fahren kann ("RNDIS").

**Timing**



Das Bild zeigt einen Zyklus von AgOpenGPS. Bestimmt wird das Timing vom Update-Zyklus des RTK-Empfängers, also ungefähr 100ms beim F9P, der auf dem Ardusimple-Board verbaut ist. Die gesendeten Positionsdaten sind also eine Mittelung über die letzten 100ms (ms = Millisekunden) und somit beim Empfang bereits 50ms "alt". Nachdem die Daten im Computer angekommen sind, berechnet AgOpenGPS die neuen Lenkvorgaben, sendet diese und bekommt als Antwort den Wert des Lenkwinkelsensors und die Daten der IMU, falls diese mit der Central Unit verbaut sind. Das ist ziemlich suboptimal, weil diese Daten dann schon mindestens 90ms alt sind, wenn AgOpenGPS mit den Positionsdaten verrechnet.

Also ein Arduino-Nano, Software drauf ("IMU_USB_v5_0.ino") und IMU dran. Leider nein, denn nun werden die Daten zwar alle 100ms gesendet, aber völlig asynchron zu den GNSS-Daten. Das wurde erkannt und "PANDA", ein proprieterer NMEA-Datensatz erschaffen, der GNSS-Daten und IMU-Daten zusammenfasst und an AgIO sendet.

Viel einfacher ist es allerdings, einen BNO080 oder BNO085 im "RVC"-Mode zu betreiben und direkt an den PC anzuschließen. Da ist nix dazwischen und daher die Lösung, die prinzipbedingt den geringsten Jitter aufweist. Dazu wird einfach ein [USB-TTL-Seriell-Kabel wie dieses](https://de.aliexpress.com/item/32965292523.html) an die IMU angelötet: Das erste Bild zeigt ein Board mit Spannungsregler, das mit 5V versorgt wird; das zweite Bild zeigt dasselbe Bord, aber mit Umgehung des Spannungsreglers - die Spannung beträgt dann 3.05V :+1:, und auf dem dritten Bild ist ein Board ohne integrierten Spannungsregler gezeigt. Ist ein Spannungsregler vorhanden, sollte die erste Lösung verwendet werden.





Für die Freunde des Ethernets: So kann man zwei two Ardusimple oder natürlich auch einen Ardusimple und die IMU mit AgIO über ein Ethernetkabel anschließen. Gezeigt ist hier [dieses Modul](https://www.pusr.com/products/dual-UART-to-ethernet-module-usr-tcp232-e2.html), hier mit zwei [Ardusimples @ 460800Bd](https://github.com/GormR/HW_for_AgOpenGPS/tree/main/central_unit_2.0/code). 

Der rote Draht ist der der +5V-Versorgung - in Worten: fünf Volt!

Schwarz: 0V
rot: 5V
braun: 3.3V
grün: zum Ardusimple (NTRIP; RxD@AS, TxD@USR)
weiss: vom Ardusimple (NMEA data; TxD@AS, RxD@USR)


(Es wurden dieselben Farben verwendet, wie beim Beispiel des BNO08x am USB-Kabel)

Alternativ zu einer Lötverbindung kann die Verbindung auch steckbar über die [Pixhawk Stecker unter Verwendung von 0V, 5V und den beiden RX- und TX-Drähten erfolgen.](https://www.ardusimple.com/simplertk2b-hookup-guide/) Eine Versorgung mit 3,3V ist in diesem Fall nicht notwendig, aber ich würde sicherheitshalber je einen 100Ohm-Widerstand in Serie zum Signal einlöten.

Leider ist der BNO085 egal in welcher Form derzeit schwer zu beschaffen, aber ein Arduino Nano RP2040 Connect-Board hat auch ein IMU und bietet sich so als Ersatz an. Eine prototypische Implementierung gibt für AgOpenGPS gibt es [hier in diesem Github Repo](https://github.com/GormR/HW_for_AgOpenGPS/central_unit_2.0/code/Arduino_nano_connect_as_IMU/). Die IMU selbst ist sicherlich nicht schlechter als die von Bosch des BNO085, aber da kein magnetischer Sensor mit verbaut ist, ist eine Nachführung des Headingdrifts nicht unmittelbar möglich. Mittelbar geht das sicherlich irgendwass einmal über AgIO, aber auch so ist die Drift ersten Versuchen nach sehr gering.

Mit dem hinterlegten Python(!)-Script simuliert das Board einen BNO085 im RVC-Mode. Dazu wird die erweiterte AgIO benötigt. [Hier](central_unit_2.0/code/) kann man die AgIO.exe mit direktem USB-Support für IMU und F9P/Ardusimple herunterladen. Einfach die Originaldatei damit ersetzen.

----
# Projekte in diesem Repository

Alle Projekte wurde in einem robusten Aluminiumgehäuse weitgehend mit industriellen M12/M8-Steckerverbindern realisiert. Es gibt aber auch die Möglichkeit, alternativ industrielle PushIn-Steckverbinder zu verwenden.

Alle Leiterplatten wurden mit dem kostenfreien Layoutprogramm „EasyEDA“ erstellt und lassen sich so direkt online bearbeiten. 

*Folgende Projekte funktionieren zwar ohne Einschränkung an AgOpenGPS, haben aber inzwischen verbesserte Nachfolger:*

[Dokumentation Central Unit](central_unit/README.md)

[Dokumentation Rooftop Unit](rooftop_unit/README.md)

[Dokumentation Ethernet Adapter for UDP](ethernet_adapter/README.md)

**Aktuelle Mainboards**

Update der Central Unit 1.x mit einem zweiten Steckplatz für dual-Ardusimple-Lösungen. Es kann auch nur eine Teilbestückung in Auftrag gegeben werden, bei der dann jeweils nur eine reine dual-Ardusimple-Einheit oder eine reine Motortreiber/Sensor-Einheit für zwei getrennte Gehäuse hergestellt wird.



[Documentation Central Unit 2.x](central_unit_2.0/README.md)

Es gibt eine [reduzierte Bauteilliste](central_unit_2.0/production_data/BOM_CentralUnit2.3_(USB-recommended).csv) für die meistverwendete USB-Variante, die für ca. 30€ herzustellen ist, wenn sich die Bauteilpreise denn mal wieder in normalen Höhen bewegen werden (Schätzpreis bei einer Bestellung von 5 Stück). 

Teensy-basierte Central Unit mit Unterstützung von USB-PD (Laden des Computers über USB-C; leider noch kein Firmware-Support bisher):

[Dokumentation Central Unit 3.x](central_unit_3.0_Teensy/README.md)

(Dieses Board hat auch einen Steckplatz für den alternativen Bynav-GNSS-Empfänger)

# Bestellhinweise
1. SMD-bestückte Leiterplatte bestellen, z. B. beim JLCPCB für ca. 35€ wie oben im englischen Teil beschrieben. Deutschsprachige Alternativen: PCB-Pool, Aisler. Vorsicht bei JLCPCB: Es werden nur die Bauteile bestückt, die zum Bestellzeitpunkt verfügbar sind (wird aber deutlich angezeigt - Liste kann auch heruntergeladen werden).
2. Je nach gewünschter Verkabelungsvariante entweder M8 + M12-Steckverbinder und Kabel bestellen oder PushIn-Buchsen und Stecker und ein passendes Gehäuse
3. Gewünschte Zusatzmodule bestellen, z. B. Lagesensor CMPS14 als (verbesserte) Alternative zum Onboard-Lagesensor MMA8452, zweiter RTK-Empfänger, ESP32 für CAN oder Dual-RTK, hier ebenfalls beschriebene Dacheinheit, RS232-Schnittstellenwandler, etc
4. Kleinkram wie Schrauben, (USB-) Kabel, Kunststoffabstandshülsen etc bestellen

Selbst gelötet werden die Steckverbinder wie unter 2. beschrieben (einfache zu löten). 

Weitere Hinweise finden sich zum Teil bei den einzelnen Baugruppen.

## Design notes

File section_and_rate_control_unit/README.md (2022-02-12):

# Section and Rate Control Unit for AgOpenGPS
(Informationen in deutscher Sprache unten)
Top view:
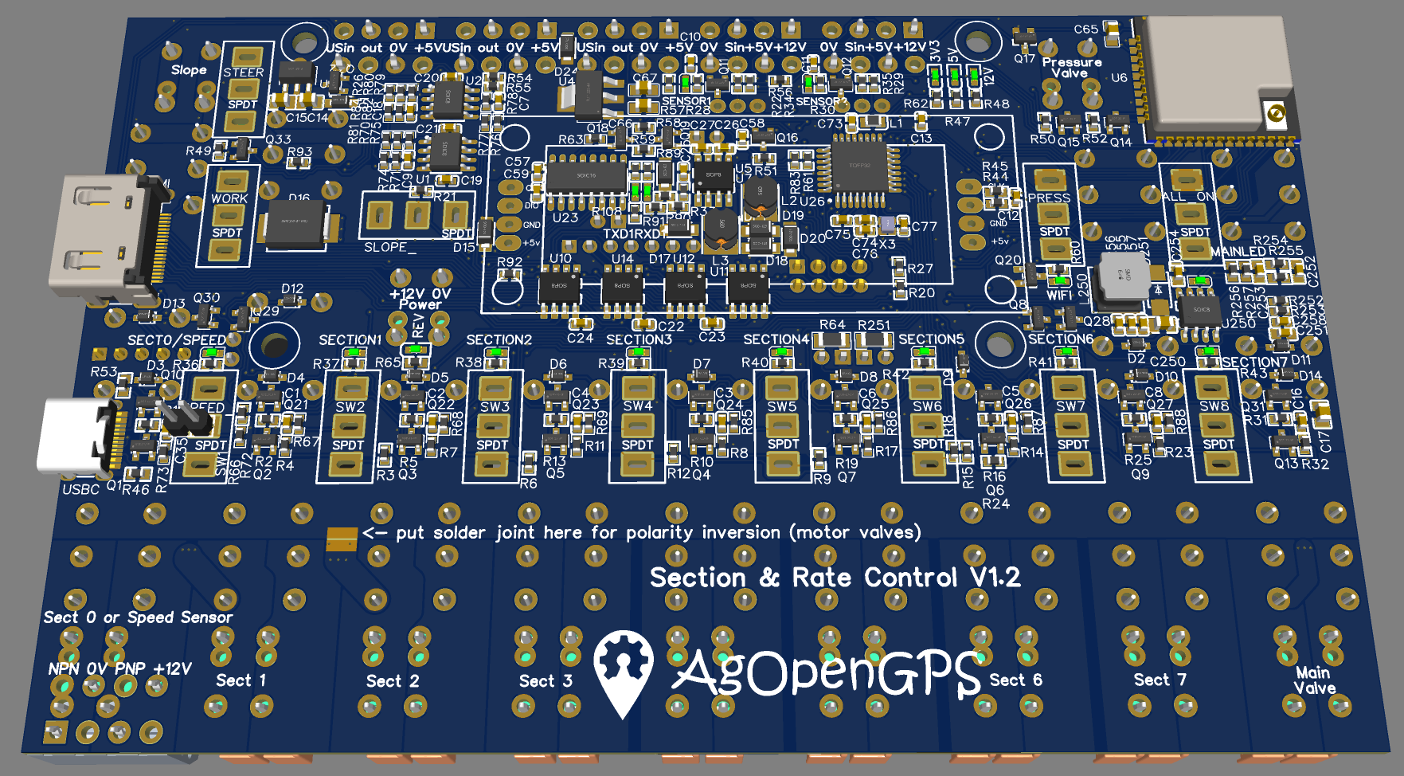
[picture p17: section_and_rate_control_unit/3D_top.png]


Bottom view:
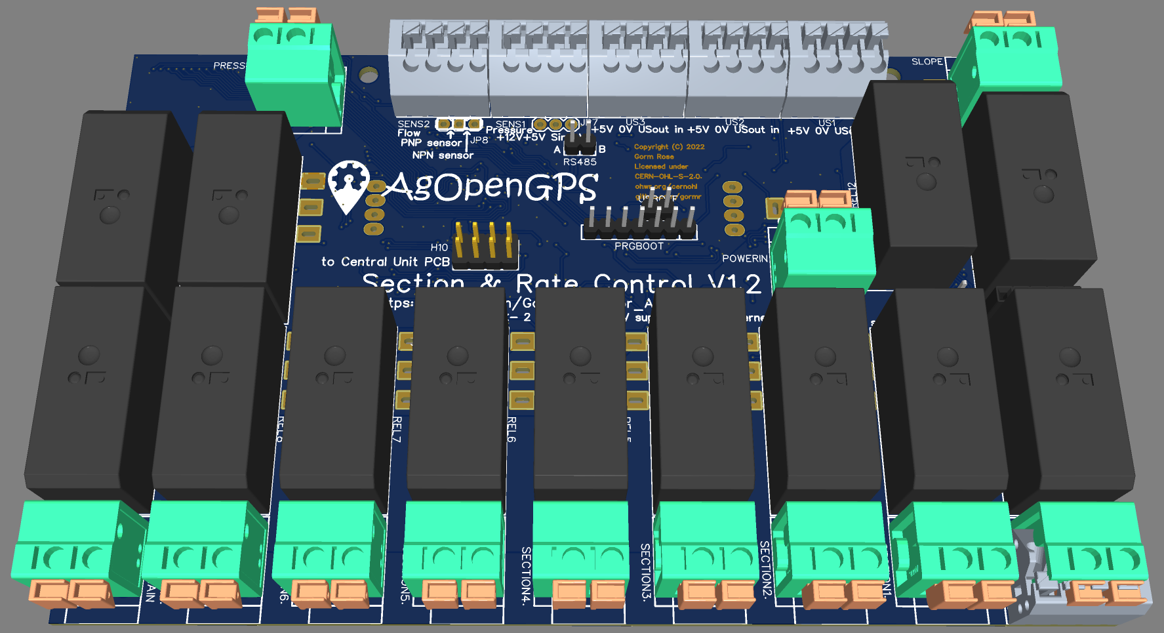
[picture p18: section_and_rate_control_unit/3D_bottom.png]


This project is a section control unit for AgOpenGPS. It is intended to be used together with the Central Unit 2.0 or Central Unit 3.0 (=Teensy) in the same or a separate housing (can be found here in Git as well). It may connected by either Ethernet, WiFi or RS485.

Brian's Concept only provided drivers for the sections w/o the possibility of manual interference. In that case, no rocker switches will be mounted, and the unit may also be located directly on the trailer.

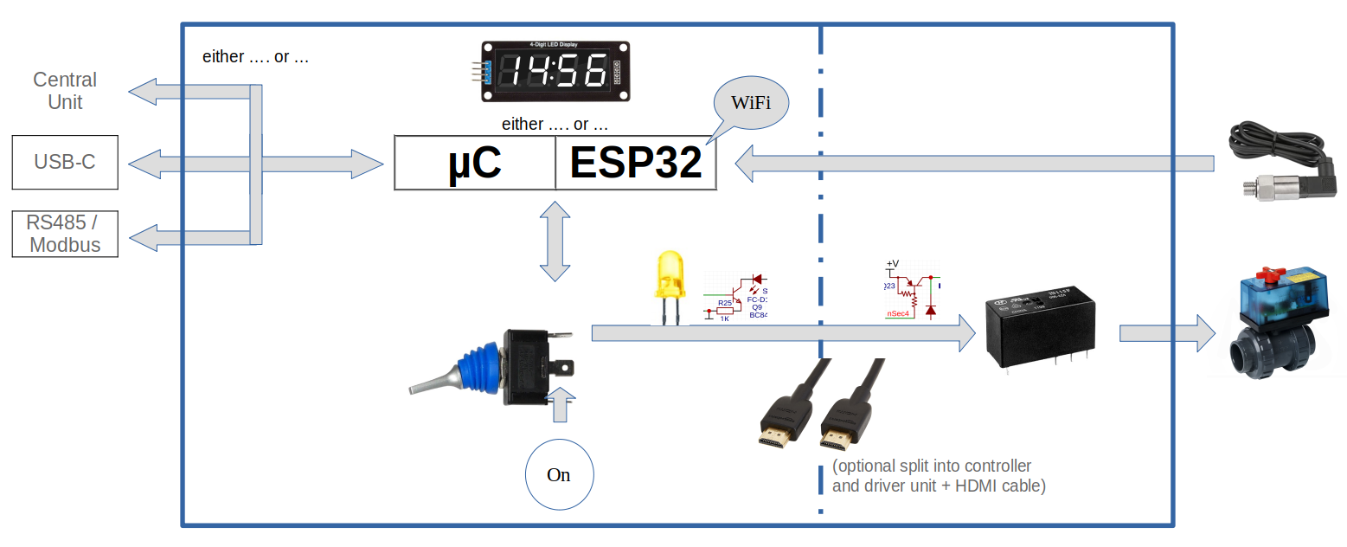
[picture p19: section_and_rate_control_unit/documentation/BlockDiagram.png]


MTZ8302 and WEder suggested a manual steering option in addition, so in general the functions provided by a Müller-Elektronik  control plus AgOpenGPS integration. To use that one or two of this PCB can be used, because both functions can either be provided on a single board or divided into two boards, of wich one contains the rocker switches and the µC and the other one (e. g. located on the trailer) the relays (and optionally another µC). If using a single µC-dual PCB solution, both units are conneced via a HDMI cable. If using two µC, options are USB, RS485, Ethernet or WiFi. 

Brian's software will work quite out-of-the box with minimal mods. MTZ8302's needs more adaptations, mainly due to the fact, that each pin can both drive the section and read back the status of the rocker switch.

- USB-C 
- Atmel section with I/Os needed for AOG
- connection to Ethernet via external module is possible
- power supply
- valves output
- RS485 / Modbus option
- ESP32 option (alternative to Atmel)

This setup does not include new functions but provides a robust, monolitic unit that may be manufactured by professionel EMS providers. 

Special focus is given to the robust housing and industrial PushIn connetors. 

# Detailed Description

In general, you can build up this unit as one (no need for the HDMI connector) or divide into a control unit that includes the µC and a power unit that might be directly on the trailer. On the power unit, you need all the parts from the schematic scheet "Machine Section Control" + parts around U3 (12V sensor supply if needed) only, and for the conrol unit on the other hand, you don't need that parts. The HDMI connector is needed on both PCBs for sure.

Heart of the section control is either an Atmel µC as U26 following [Brian's suggestion](https://github.com/farmerbriantee/AgOpenGPS/tree/master/Support/RateControl) or an ESP32 as U6 following [Matthias' suggestion](https://github.com/mtz8302/AOG_SectionControl_ESP32). For using grade control via ultrasonic sensors, the ESP32 is needed. If the ESP32 is used, X3 is not necessary and should be deleted from the BOM in order to avoid additional costs. Do not mount both µCs!

No matter what µC you wanna use, I follow Matthias' idea, that a manual control of the sections should be possible in any case. This is done with the switches SW1..SW8 for 8 different sections maximum. Mount less switches for less sections of course. The priciple is the following: If using an on-off-on switch, you can either switch to "1" (via main switch), "0" or the µC output for AgOpenGPS control. In any case, the µC can read back that status by temporary switching it's I/O pin to input. The output status is stored in the caps C1..C8 for that moment. R1 and Q1 (for channel 0) are a constant current sink, so that common mode voltages do not matter, if you have your power unit on the trailer. That is also the separation between the power drawn from USB (control voltages) and the direct 12V power supply used for the output relays, so that any miswiring of the power section cannot kill any USB-related parts or the tablet.

In order to safe wires, the signals for pressure up/down and slope control are tristate signals: "0", high-impedance, "1". With the help of the comparators U1 and U2, this is tranfered into 2 bits each for the relay control again. U1 and U2 have open collector outputs, so that they can sink the relay driving transistors connected to 12V directly. Same priciple as with Q1..Q8.

Mind that there is intentionally no connection between the USB voltage and the power stage supply voltage. In case, your tablet is fully isolated from the tractor power system (e. g. by using an power inverter + AC/DC charger or running from battery), the 12V LED will now light even if 12V is connected and the 5V LED is lighting; you need to close jumper "ON1" to connect 0V (USB) with 0V (power stage):

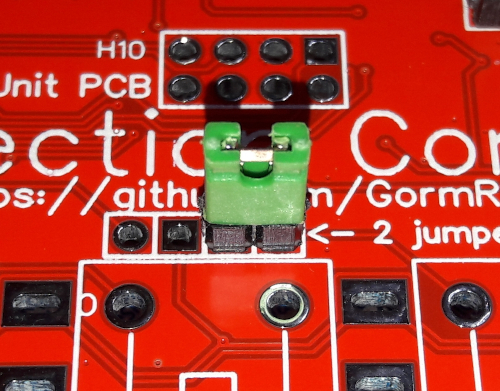
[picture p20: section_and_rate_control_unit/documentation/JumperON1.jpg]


The relays do the power driving. Yes, old style, but simple and available right now. They can control electromagnetic valves (power on = flow on) or motor-controlled valves (one polarity = flow on, other polarity = flow off). For that, set one solder bridge on the board (on top side, between REL2 and REL3).

All actuators are connected to the connectors next to the relays. Suggestest type: [Weidmueller LSF-SMT 5.08/02/90 3.5SN](https://catalog.weidmueller.com/catalog/Start.do?localeId=en&ObjectID=1824810000) or [Weidmueller LSF-SMT 5.00/02/135 3.5SN](https://catalog.weidmueller.com/catalog/Start.do?localeId=en&ObjectID=1884340000). Or the China ones in the BOM, but don't complain... ;)

Sensors may be used for pressure, flow and optionally for speed pulses. In that case, only 7 sections are available and you must not mount the jumper "REL" next to switch "SW1".

The sensors may be supplied with 5V (from USB - they need only some mA) or 12V (U3 works as short circuit protection). Suggestest connector type here: [Weidmueller LSF-SMT 3.50/04/180 3.5SN BK TU](https://catalog.weidmueller.com/catalog/Start.do?localeId=en&ObjectID=1825660000) or [Weidmueller LSF-SMT 3.50/04/135 3.5SN](https://catalog.weidmueller.com/catalog/Start.do?localeId=en&ObjectID=1885670000). Or again the China ones in the BOM, but don't complain... ;) 

When using Ethernet/Wifi only, the power supply around U250 is needed. If not, delete U250, L250, D251 and C250..C258 from the BOM to safe money.

Same is true for U4, which is only needed for the ESP32. If no ESP32, delete U4 and C65..C67 from BOM.

Control data interface:
USB is needed if using an ESP32 - at least for programming. Suggested is the USB-C plug, but you can also connect [external connectors](https://www.aliexpress.com/item/1005002859111621.html) to CN3.

For serial data communication while in use or programming (Atmel only), you can use either USB or RS485 (most reliable) or - if you have it in the same box as the centrol board - TTL-serial directly via H10. If using RS485, you need U5 and U23 must be either unmounted or the jumper "USBOFF" must be set. If you're using USB, you can delete U5 in the BOM to safe money; if you're using RS485 or H10, you may delete all U23, U5 and USBC as long as you don't need it for programming.

DP1 is optional for displaying things like pressure, etc. 

There's no use for U10..U14 today, as there is not PWM power stage designed yet. Let's see next year..

The initial programming of the Atmel (if any) is done via "PRGBOOT". [Please refer to this how-to.](https://www.arduino.cc/en/Tutorial/BuiltInExamples/ArduinoISP).

Finally, the steer and work switches may be used for AgOpenGPS steering, if this PCB in mounted inside the same box.

# 150 x 100 mm² 
2-layer 70 or 35µm, 1,6mm thickness, technology: 0.2mm/0.2mm/0.3mm; SMD assembly: 72 different parts, 252 parts overall, THT: only relays, 2.54mm headers and plugs 

[Link to EasyEDA project](https://oshwlab.com/GoRoNb/aog_io-box_copy). The pick-and-place data in the [production data](production_data) is already rotated correctly for JLC.

# Functions in-cabin-unit for section control
- integrated Arduino-Nano hardware
- ESP32-Module option
- 8 valve outputs (relays)
- +/- pressure output
- slope control output
- Steer/Work switch for AgOpenGPS
- LED display
- mounting holes
- USB-C / WiFi / RS485 / (Ethernet)
- virtual serial port for RS485/ModbusRTU
- many LEDs
- Ethernet/UDP option 
- WIFI option via ESP32

These [connections](Connections.pdf) are provided:
- Supply 12V/24V (optional)
- USB-C to tablet/notebook
- RS485/ModbusRTU
- USB-C
- Ethernet module (cable to connector PRGBOOT)

# Initial Operation Instructions
1. if applicable: [assemble missing SMD parts](https://www.youtube.com/watch?v=dLczChhmDCY)
2. assemble all THT parts: pin headers and connectors
3. Atmel µC: apply 5V e. g. via USB (current should be about 22mA w/o U10, U11, U12 and U14). ESP32: Slowly increase input voltage on USB and with current limit of 100mA while checking the 3.3V voltage; +3.3V must not rise up to more than 3.4V!If U250 is mounted: Slowly increase input voltage on 12V input with jumpers "ON1" and "ON2" closed: 0mA@7V, 17mA@8V (Atmel), 15mA@12V, 9mA@20V; 3.3V must not rise up to more than 3.4V, 5V not to 5.1V. 
4. connect Arduino Uno board and flash bootloader via "PRGBOOT" (https://www.arduino.cc/en/Tutorial/BuiltInExamples/ArduinoISP) 
5. disconnect Uno board and connect USB (if available): The PC should display a new USB virtual serial device based on CH340 
6. flash Atmel/ESP32 via Arduino software
7. connect sensors, etc do a test with AgOpenGPS

Connection for initial programming:
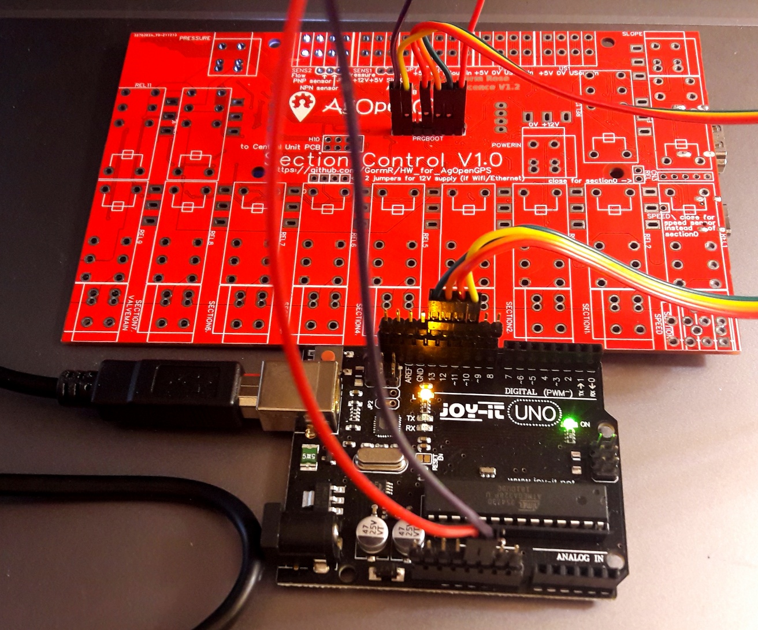
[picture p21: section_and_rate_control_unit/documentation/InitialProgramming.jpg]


debugging: use terminal like HTerm and find out the correct COM port: connect to each possible one, set "DTR" and release "DTR". When releasing, the red LED blinks 3 times (bootloader). The green LED next to U3 will blink when sending any serial data to the Nano; this is also true when sending with the Arduino IDE (serial monitor)

Further information are also provided in the upper folder.

There is also an [English user group](t.me/agopengpsinternational) and a [multilingual forum](https://discourse.agopengps.com/t/section-control-for-the-central-unit/7779/10?u=goronb). 

----------------------------------------------------------------------------------------------------------------------------

# Übersicht

Bei diesem Board handelt es sich um eine Section-Control-Steuerung für AgOpenGPS. Sie kann zusammen mit der Central Unit 2.0 oder Central Unit 3.0 (=Teensy) in einem Gehäuse verbaut werden oder eben auch nicht. Ein Anbindung über Ethernet, WiFi oder RS485 ist auch möglich.

Brian's Konzept sieht lediglich eine Ansteuerung der Section ohne weitere Eingriffsmöglichkeit vor. In dem Fall werden keine Schalter bestückt, und die Einheit kann ggf. auf der Anhängespritze selbst angebaut werden.

MTZ8302 bzw WEder schlagen ergänzend die Möglichkeit einer alternativen Handsteuerung vor, also im Prinzip das, was eine Müller-Elektronik-Steuerung leistet plus die Einbindung in AgOpenGPS. Hierzu können ein- oder zwei Leiterplatten verwendet werden, da sich sowohl beide Funktionalitäten in einem Board bestücken lassen, als auch separat, also z. B. die Leiterplatte mit den Schaltern im Traktor und dieselbe Leiterplatte mit Relais bestückt im Trailer. Dabei kann sowohl eine ein-µC-Lösung gewählt werden, bei der das Relais-Modul via HDMI-Kabel verbunden wird, als auch eine zwei-µC-Lösung mit USB, RS485, Ethernet oder WiFi. 

Die Software von Brian läuft auf dem Atmel ohne große Änderungen. Die Software von MTZ8302 muss allerdings angepasst werden, da an einem Pin sowohl die passende section aktiviert wird, als auch der zugeordnete Schalter zurückgelesen wird.

# Schaltungsbeschreibung (Copy of English text)

Die Teilbreitensteuerung kann als eine Einheit aufgebaut werden (bei der dann keine HDMI-Buchse benötigt wird) oder in Kontrolleinheit und Leistungsteil getrennt werden, falls man z. B. den Leistungsteil direkt auf dem Spritzenanhänger anbringen möchte. Für den Leistungsteil muss nur alles bestückt sein, was sich auf dem Schaltplanblatt "Machine Section Control" befindet + die Bauteile um U3 (Sensorversorgung 12V falls benötigt). Auf dem Controlboard werden diese Teile dann nicht benötigt. Die HDMI-Buchse muss natürlich auf beiden drauf sein..

Kern der Schaltung ist entweder ein Atmel µC (U26), wie von [Brian vorgeschlagen](https://github.com/farmerbriantee/AgOpenGPS/tree/master/Support/RateControl) oder ein ESP32 (U6), wenn man [Matthias' Vorschlag](https://github.com/mtz8302/AOG_SectionControl_ESP32) folgt. Möchte man eine automatische Handneigungsverstellung mit Ultraschallsensoren nutzen, muss ein ESP32 verwendet werden. Wenn ein ESP32 benutze wird, wird X3 nicht benötigt und kann in der BOM gelöscht werden, um Bestückkosten zu sparen. Nicht beide µC bestücken!!

Unabhängig vom verwendeten µC stimme ich mit Matthias überein, dass eine manuelle Kontrolle der Teilbreiten und damit ein Betrieb ohne AgOpenGPS jederzeit möglich sein sollte. Acht Teilbreiten sind maximal möglich (mit Geschwindigkeitssensor sieben). SW1..SW8 sind An-Aus-An-Taster und schalten zwischen "1" (über Gesamtschalter), "0" und Automatikbetrieb um. Dazu kann der µC seine I/Os kurz auf Eingang umschalten und dann den Zustand zurücklesen, der in den Kondensatoren C1..C8 "gespeichert" wird. R1 und Q1 (am Beispiel der ersten Teilbreite) bilden eine Konstantspannungssenke mit hoher Gleichtaktfestigkeit und trennen somit den von USB versorgten Bereich (µC und Co) vom Leistungsteil, so dass Fehler im Leistungsteil nicht am µC oder Tablet zerstören können.

Deshalb sind die Versorgungsspannungen von USB und Leistungsendstufe bewusst unverbunden. Wenn also das Tablet vollkommen potentialfrei betrieben wird (z. B. Akkubetrieb oder Steckernetzteil + 230V-Inverter), wird selbst bei angeschlossenen 12V die 12V-LED nicht leuchten, wenn die 5V LED leuchtet, und es muss Jumper "ON1" geschlossen sein (Bild):



Um Verbindungsleitungen zu sparen, werden für die Druck- und Hangneigungsverstellung 3 Zustände pro Draht übertragen: "0", hochohmig, "1". Mit Hilfe der Komparatoren U1 und U2, die open-collector-Ausgänge haben, werden dann wieder die jeweils 2 Relais angesteuert genauso wie die Teilbreiten über Q1..Q8.

Hier werden Relais für die Ansteuerung der Teilbreiten benutzt, was eigentlich nicht mehr Stand der Technik ist, aber gerade die Bauteile der Wahl sind, weil Endstufenhalbleiter nicht beschaffbar sind. Es muss ja auch noch etwas für nächstes Jahr zu tun geben...

Es können sowohl elektromagnetische Ventile (Spannung an = Düse an) oder auch Motorventile (Düse ist je nach Polarität an oder aus) verwendet werden. Für Motorventile muss die Lötbrücke auf der Oberseite der Leiterplatte zwischen REL2 und REL3 geschlossen werden (Lötpunkt).

Die Aktoren werden über die Steckverbinder neben den Relais angeschlossen. Mein Vorschlag: [Weidmueller LSF-SMT 5.08/02/90 3.5SN](https://catalog.weidmueller.com/catalog/Start.do?localeId=en&ObjectID=1824810000) oder [Weidmueller LSF-SMT 5.00/02/135 3.5SN](https://catalog.weidmueller.com/catalog/Start.do?localeId=en&ObjectID=1884340000). China geht auch, aber bitte nicht über unzuverlässige Kontakte beschweren... ;)

Sensoren sind vorgesehen für Druck, Druchfluss und optional für Geschwindigkeitspulse. Bei letzterem sind dann "nur" 7 Teilbreiten möglich und der Jumper "REL" darf nicht gesetzt sein. Am besten in dem Fall gleich das Relais "REL1" weglassen.

Die Sensoren werden aus den 5V des USB-Ports versorgt - sie brauchen ja nur ein paar mA oder aus 12V (hier sorgt U3 für den notwendigen Kurzsschlussschutz). Vorschläge für Steckverbinder hier: [Weidmueller LSF-SMT 3.50/04/180 3.5SN BK TU](https://catalog.weidmueller.com/catalog/Start.do?localeId=en&ObjectID=1825660000) oder [Weidmueller LSF-SMT 3.50/04/135 3.5SN](https://catalog.weidmueller.com/catalog/Start.do?localeId=en&ObjectID=1885670000). China geht ebenfalls; es gilt das oben gesagte.. ;) 

Wenn zum Betrieb Ethernet/Wifi verwendet werden soll, muss die Stromversorgung um U250 bestückt sein. Sonst bitte U250, L250, D251 und C250..C258 in der BOM löschen, um Bestückkosten zu sparen.

Gleiches gilt für U4, das nur für den ESP32 benötigt wird. Wenn keiner verwendet wird, hier U4 und C65..C67 in der BOM löschen.

Verbindung zu AgOpenGPS:
USB wird immer benötigt, wenn ein ESP32 verwendet wird - mindestens zur initialen Programmierung. Ich schlage eine USB-C-Buchse vor, aber man kann auch einen [externen Connector](https://www.aliexpress.com/item/1005002859111621.html) an CN3 anschließen.

Die Kommunikation im Betrieb oder zum Programmieren (nur für den Atmel) kann entweder über USB oder RS485 erfolgen oder - wenn das Board im der gleichen Kiste wie die Zentraleinheit steckt - über Steckverbinder H10 direkt als TTL-Signal. Für RS485 muss U5 bestückt sein und U23 entweder unbestückt sein oder der Jumper "USBOFF" ist gesetzt. Falls USB nicht benötigt wird, einfach U5 in der BOM löschen. Wenn die Kommunikation über H10 erfolgt, können U23, U5 und USBC gelöscht werden, falls nicht zum Programmieren benötigt.

DP1 ist optional, um ein paar nette Dinge wie Druck, etc anzeigen zu können. 

U10..U14 haben keine Verwendung bis jetzt (können also in der BOM gelöscht werden), solange keine PWM-Leistungsentstufe existiert. Das ist was für nächstes Jahr..

Für die initiale Programmierung des Atmels (falls vorhanden) wird "PRGBOOT" verwendet. [Hier gibt es ein nettes Tutorial.](https://www.arduino.cc/en/Tutorial/BuiltInExamples/ArduinoISP).

Zu guter Letzt gibt es noch die beiden Schalter STEER und WORK, die direkt mit der Autosteer-Einheit verbunden werden können. Sonst einfach weglassen.

# Erstinbetriebnahme
1. Ggf. fehlende SMD-Bauteile [nachbestücken](https://www.youtube.com/watch?v=dLczChhmDCY)
2. gewünschte Stiftleisten und Stecker auflöten
3. langsam die Spannung an USB mit einer Strombegrenzung von 100mA bis max. 5V hochregeln und gleichzeit die 3.3V-Spannung im Auge behalten
4. +3.3V überprüfen (sollte im Bereich 3.2..3.4V sein)
5. Arduino-Uno-Board mit "PRGBOOT" verbinden und Bootloader flashen (https://www.arduino.cc/en/Tutorial/BuiltInExamples/ArduinoISP) 
6. Uno-Board abstöpseln
7. über USB mit einem PC verbinden: Der PC muss einen neue virtuelle serielle Schnittstelle auf CH340-Basis anzeigen)
8. Code wie gewohnt mit der Arduino-Software flashen
9. Sensoren anschliessen und mit AgOpenGPS testen

debugging: use terminal like HTerm and find out the correct COM port: connect to each possible one, set "DTR" and release "DTR". When releasing, the red LED blinks 3 times (bootloader). The green LED next to U3 will blink when sending any serial data to the Nano; this is also true when sending with the Arduino IDE (serial monitor)

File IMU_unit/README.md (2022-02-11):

# IMU Unit for AgOpenGPS/QtOpenGuidance  
(Informationen in deutscher Sprache unten)
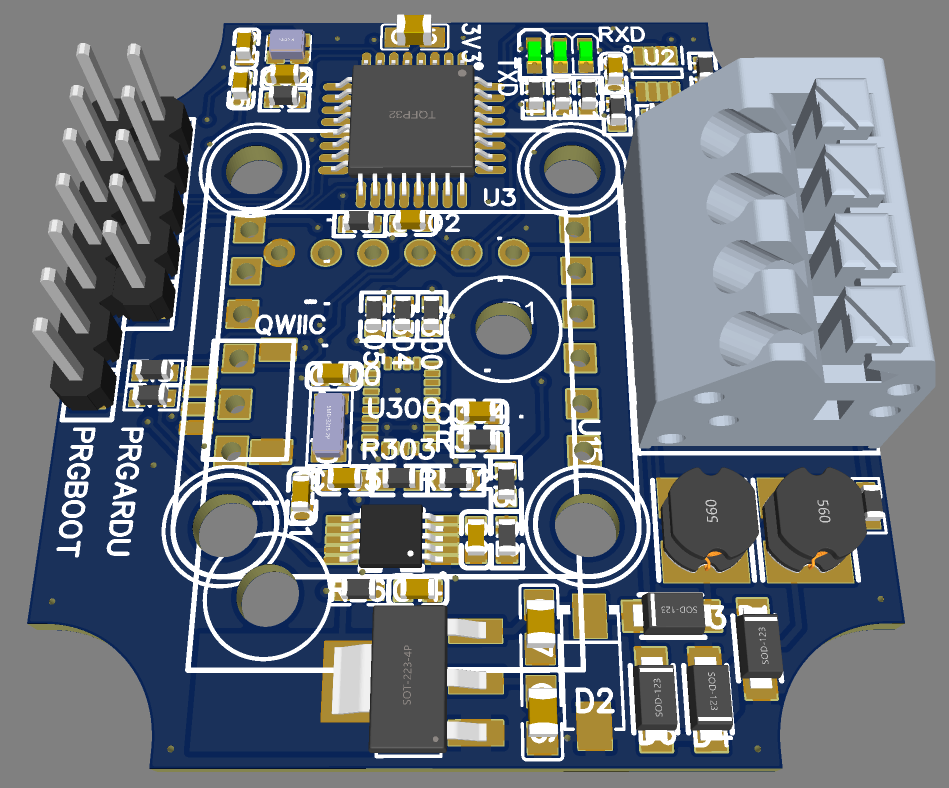
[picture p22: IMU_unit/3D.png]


This project is an IMU unit for AgOpenGPS, working via a fool-proof two-wire twisted pair bus for power and data. It will be connectable to the central units 2 & 3 in the future.

Functions' overview:

- Atmel section 
- power supply
- WAS input
- IMU

Special focus is given to the robust housing. PushIn connectors may also be used for single wire connections).

# 42 x 42 mm² 
2-layer 35µm, 1,6mm thickness, technology: 0.15mm/0.15mm/0.3mm; SMD assembly

[Link to EasyEDA project](https://oshwlab.com/GoRoNb/imu-for-agopengps). The pick-and-place data in the [production data](production_data) is already rotated correctly for JLC.

# Functions in-cabin-unit for autosteering (all SMD + THT connectors)
- integrated Arduino-Nano hardware
- ADC (ADS1115) for wheel angle sensor (WAS)
- BNO085 option (as CMPS14 board)
- many LEDs

These [connections](Connections.pdf) are provided:
- Wheel angle sensor (WAS)
- 2-wire bus

# Initial Operation Instructions
0. [read changelog](changelog.txt)
1. if applicable: [assemble missing SMD parts](https://www.youtube.com/watch?v=dLczChhmDCY)
2. assemble alls THT parts: pin headers and connectors
3. slowly increase input voltage on +5V with a current limit of 30mA while checking the 3.3V voltage; +3.3V must not rise up to more than 3.4V!)
4. connect Arduino Uno board and flash bootloader via PRGBOOT connector (https://www.arduino.cc/en/Tutorial/BuiltInExamples/ArduinoISP)* 
5. disconnect Uno board and connect an USB-serial-adapter with 3.3V signals to the connector "PRGARDU"
6. flash [firmware](code) via Arduino software => blue TXD3-LED starts flashing (the firmware is a copy of [BrianTee's Arduino code](https://github.com/farmerbriantee/AgOpenGPS/blob/master/Support_Files.zip) with mods to support RS485 data flow steering)
7. test with AgOpenGPS with the help of an [powerlink USB stick](https://github.com/GormR/RS485-OOK-USB-Adapter) or [Central Unit 2.x](https://github.com/GormR/HW_for_AgOpenGPS/tree/main/central_unit_2.0) or [Central Unit 3.x](https://github.com/GormR/HW_for_AgOpenGPS/tree/main/central_unit_3.0_Teensy)

*_ either with a 3.3V-Arduino or Uno with adapter ( [1k in each signal line + additional diode in _reset line](documentation/adapter_for_Arduino_Uno.jpg) ) 

There is also an [English user group](t.me/agopengpsinternational) and a [multilingual forum](https://github.com/GormR/HW_for_AgOpenGPS/tree/main/central_unit_2.0). 

----------------------------------------------------------------------------------------------------------------------------

# Functional Description (to be continued..)

All voltage and I/O functions are equipped with LEDs.

The PCB project was set up with the EDA program „EasyEDA“, which is freely usable. 

# (German copy) Zusammenfassung

Dieses Projekt ist eine kompakte IMU-Unit für AgOpenGPS.

Besonderer Wert wurde auf ein robustes Gehäuse gelegt. 

Folgende Funktionen sind vorgesehen:

- integrierte Arduino-Nano-Hardware
- ADC (ADS1115) für Lenkwinkelsensor
- Neigungssensor (BNO085/CMPS14)
- QWIIC für I²C-Kram

# Im Detail 

(wird fortlaufend ergänzt, allerdings meistens zunächst der englische Teil)

Das Leiterplattenprojekt wurde im frei verfügbaren EDA-Programm „EasyEDA“ erstellt. 

[Link zum EasyEDA-Projekt](https://oshwlab.com/GoRoNb/imu-for-agopengps)

Weitere allgemeine Informationen finden sich auch im übergeordneten Ordner.

Hilfestellung gibt es auch in der  [deutschsprachigen Nutzergruppe](t.me/AGOpenGPSGerman) und im [mehrsprachigen Forum](). 

# Erstinbetriebnahme
1. Ggf. fehlende SMD-Bauteile [nachbestücken](https://www.youtube.com/watch?v=dLczChhmDCY)
2. gewünschte Stiftleisten und Stecker auflöten
3. langsam die Spannung an CN4/POWER mit einer Strombegrenzung von 100mA hochregeln und gleichzeit die 5V-Spannung im Auge behalten (Eingangsstrom: 0mA bis ca. 4V, 20mA @ 4.5V, 12mA @ 12V; +5V darf nicht über 5,1V ansteigen!)
4. +3.3V überprüfen (sollte im Bereich 3.2..3.4V sein)
5. Arduino-Uno-Board mit P1 verbinden und Bootloader flashen (https://www.arduino.cc/en/Tutorial/BuiltInExamples/ArduinoISP) 
6. Uno-Board abstöpseln
7. [BrianTee's Arduino-Code](https://github.com/farmerbriantee/AgOpenGPS/blob/master/Support_Files.zip) wie gewohnt mit der Arduino-Software flashen
9. Lenkwinkelsensor (auch als WAS oder LWS bezeichnet) anschliessen und mit AgOpenGPS testen

# Component Sources (examples) / Beispiele Bezugsquellen:

(see [BOM-THT](production_data) for further information)

PushIn:		  Weidmueller [S2C-SMT 3.50/04/180G 3.5SN BK BX](https://catalog.weidmueller.com/catalog/Start.do?localeId=en&ObjectID=1290030000) + [B2CF 3.50/04/180 SN OR BX](https://catalog.weidmueller.com/catalog/Start.do?localeId=en&ObjectID=1277270000) via [Conrad](https://www.conrad.com)/[digikey](https://www.digikey.com)

(see [BOM-THT](production_data) for further information)

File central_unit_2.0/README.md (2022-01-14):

# Central Unit V 2.0 AgOpenGPS/QtOpenGuidance  
(Informationen in deutscher Sprache unten)


This project includes all hardware function that are needed to run AgOpenGPS on one board. A 2nd board is only needed for Section Control, which can be placed inside the same housing. This setup does not include new functions but provides a robust, monolitic unit that may be manufactured by professionel EMS providers. The central unit V2.0 is compatible to [BrianTee‘s Nano firmware](https://github.com/farmerbriantee/AgOpenGPS/releases/download/5.4.7/SupportFiles.zip) and to my [improved version](code/Autosteer_USB_CMPS14_low_jitter_twistable/). The ESP32 option is compatible with MTZ8002's code as long as USB is used. The project is an update of the Central Unit V1.x which may still be used for single-RTK AgOpenGPS setups w/o limitations.

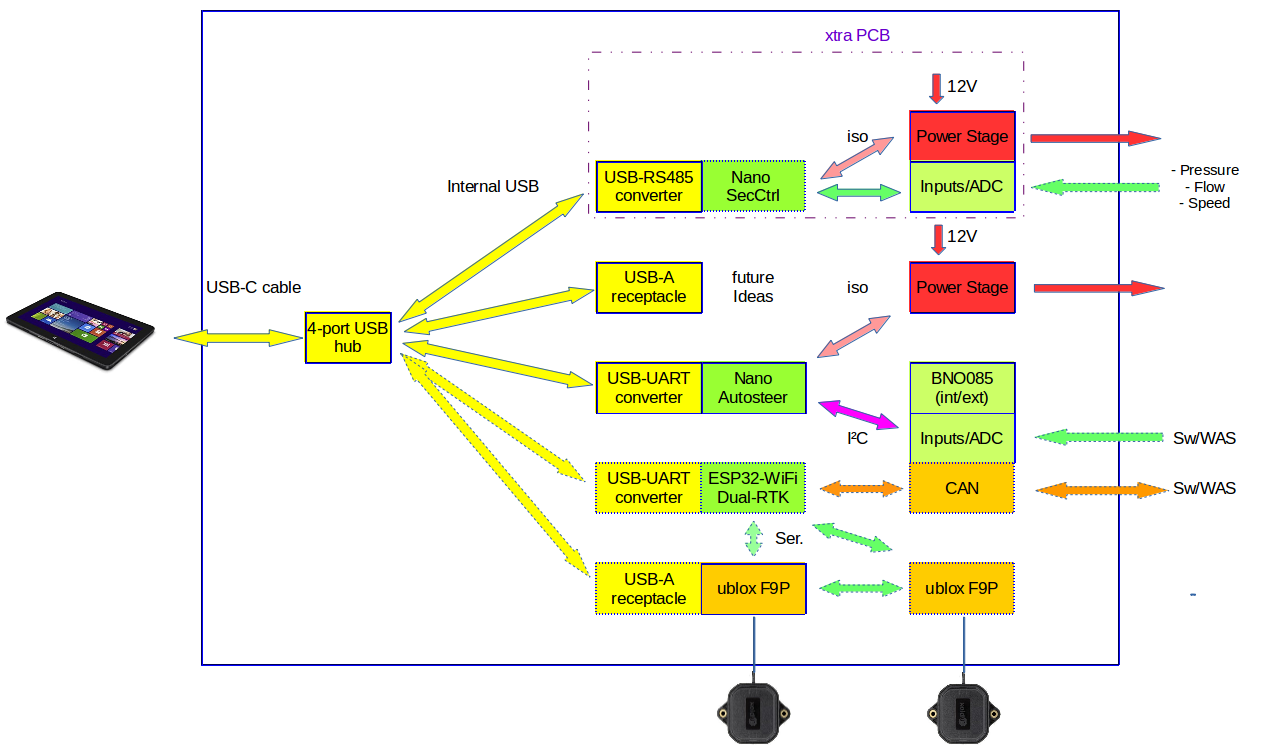
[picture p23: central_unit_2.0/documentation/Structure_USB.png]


The [drawings/Structure_USB.png](block diagram) for USB shows the 4-port USB hub on the left side providing 4 links:

1. virtual COM-Port for Atmel (Steering; provides Arduino Nano functionalities)
2. RTK-GNSS for positioning; either one directly connected Ardusimple board or the ESP32 via a virtual COM port like suggested by [AOG_Autosteer_ESP32](https://github.com/mtz8302/AOG_Autosteer_ESP32).
3. virtual COM port for Section Control (routed to a connector to the Section Control module (see subfolder here in Github, please)
4. USB receptacle for general propose (e. g. 5G stick, external MEMS, etc)

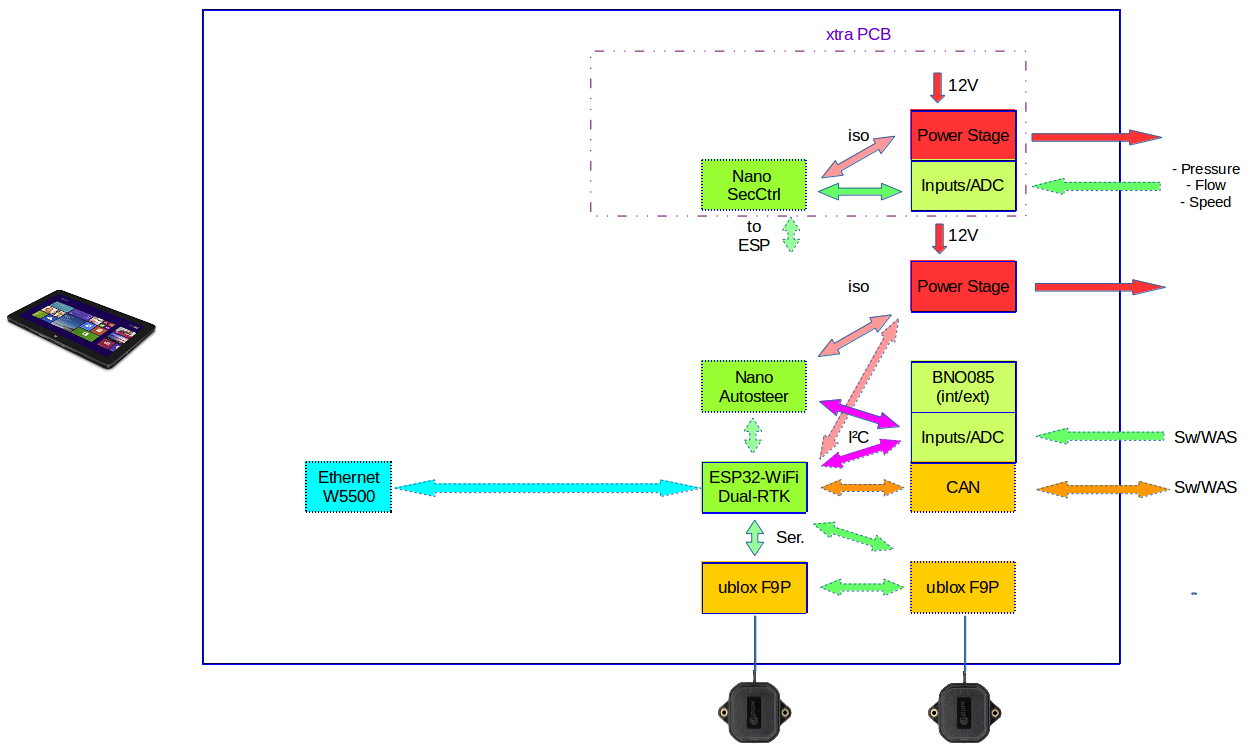
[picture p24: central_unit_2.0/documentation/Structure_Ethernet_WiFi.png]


For [drawings/Structure_Ethernet_WiFi.png](Ethernet), the W5500 has to be mounted and the software has to be adapted. Possibles solutions are both a  single-µC solution and a dual-core solution with ESP32 and Atmel, in which the ESP32 has to distribute the data sets. In that case, the 12V-to-5V power supply must be mounted, too, to generate the power for the logic. The same is true for WiFi.

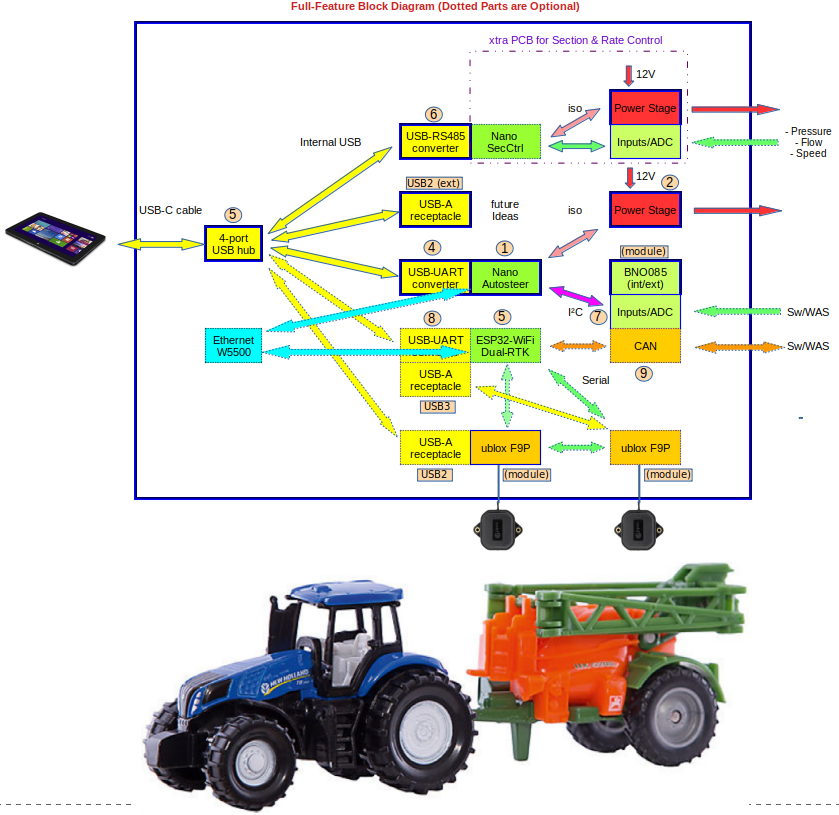
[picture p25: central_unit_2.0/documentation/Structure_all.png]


The [drawings/Structure_all.png](full block diagram) looks a little bit ugly. All components can be mounted anyway and the choice of the final setup can be made later on. By placing the USB receptacle for the Ardusimple, the virtual COM-Port for dual-RTK is automatically deactivated e. g. 

Functions' overview:

- USB hub, USB devices, USB-C 
- Atmel section with I/Os needed for AOG
- connection to Ethernet
- power supply
- motor driver incl. current feedback
- WAS input
- RS485 / Modbus
- CAN
- ESP32 option

Special focus is given to the robust housing and industrial M12/M8 connetors (optional). PushIn connectors may also be used for single wire connections).

# 160 x 100 mm² 
2-layer 35µm, 1,6mm thickness, technology: 0.15mm/0.15mm/0.3mm; SMD assembly: 72 different parts, 252 parts overall, THT: only 2.54mm headers and plugs of your choice

[Link to EasyEDA project](https://easyeda.com/GoRoNb/aog_io-box). The pick-and-place data in the [production data](production_data) is already rotated correctly for JLC.

# Functions in-cabin-unit for autosteering (all SMD + THT connectors)
- integrated Arduino-Nano hardware
- ESP32-Module (Arduino Firmware has to be adapted)
- ADC (ADS1115) for wheel angle sensor (WAS)
- BNO085 option (as CMPS14 board)
- motor driver (H-bridge of IBT-2) with 2-channel switch-off
- current feedback from motor driver (may be used to quit autosteering on driver interaction)
- 2 protected digital inputs (WORK usable as analog input, too)
- one optional digital optoisolated output
- mounting holes for RKT unit board(s) (for dual-RTK)
- USB hub (4-port)
- CAN via ESP32
- virtual serial port for RS485/ModbusRTU
- many LEDs
- Ethernet/UDP option 
- WIFI option via ESP32

These [connections](Connections.pdf) are provided:
- Supply 12V/24V (optional for motor)
- USB-C to tablet/notebook
- Wheel angle sensor (WAS)
- Digital inputs
- USB for 5G stick for IMU
- Steering wheel motor / hydraulic unit
- CAN2.0
- RS485/ModbusRTU
- Incremental sensor for steering wheel
- USB-C
- QWIIC connector
- internal USB connectors
- RJ45 for Ethernet

# Initial Operation Instructions
0. [read changelog](changelog.txt)
1. if applicable: [assemble missing SMD parts](https://www.youtube.com/watch?v=dLczChhmDCY)
2. assemble alls THT parts: pin headers and connectors
3. slowly increase input voltage on CN4/POWER with current limit of 100mA while checking the 5V voltage (should be 0mA till about 4V, 20mA @ 4.5V, 12mA @ 12V; +5V must not rise up to more than 5.1V!)
4. check +3.3V (should be in the range 3.2..3.4V)
5. connect Arduino Uno board and flash bootloader via PRGBOOT (https://www.arduino.cc/en/Tutorial/BuiltInExamples/ArduinoISP)* 
6. disconnect Uno board and connect USB (either CN2 or CN13/CN8/USB-C): The PC should display a new USB hub at least one several serial device 
7. flash [BrianTee's Arduino code](https://github.com/farmerbriantee/AgOpenGPS/blob/master/Support_Files.zip) via Arduino software => blue TXD3-LED starts flashing
8. connect WAS, buttons, motor and do a test with AgOpenGPS

*_ either with a 3.3V-Arduino or Uno with adapter ( [1k in each signal line + additional diode in _reset line](documentation/adapter_for_Arduino_Uno.jpg) ) 

Accessing the ESP32 words with Arduino as well e. g. as "LOLIN D32".

When using the ESP32 as dual-RTK-receiver, mind setup information [for Ardusimple boards provided by MTZ8302](https://github.com/mtz8302/AOG_GPS_ESP32). Change two lines of the source code:

byte LEDWiFi_PIN = 15;      // WiFi Status LED 0 = off (default: = 2)

byte DataTransVia = 1;      //transfer data via 0 = USB / 1 = USB 10 byte 2x / 7 = UDP / 8 = UDP 2x (default = 8)

Alternatively, this can be done in the web interface of AOG_GPS_ESP32 @ 192.168.1.1 (SSID: "GPS_unit_F9P_Net")

The setup process for the Ardusimples is shown [here](documentation/setup_Ardusimple). The config files are the ones provided by MTZ8302.

Some currents:
out of the box with Atmel and ESP32: 200mA@9V,   153mA@12V,   124mA@15V
with 2 additional Ardusimples:       310mA@9V,   238mA@12V,   195mA@15V
()if supplied via USB: 250mA and 470mA)

debugging: use terminal like HTerm and find out the correct COM port: connect to each possible one, set "DTR" and release "DTR". When releasing, the red LED blinks 3 times (bootloader). The green LED next to U3 will blink when sending any serial data to the Nano; this is also true when sending with the Arduino IDE (serial monitor)

Further information are also provided in the upper folder.

There is also an [English user group](t.me/agopengpsinternational) and a [multilingual forum](https://github.com/GormR/HW_for_AgOpenGPS/tree/main/central_unit_2.0). 

----------------------------------------------------------------------------------------------------------------------------

# Functional Description

The Arduino part including roll sensor, ADC and digital inputs is a copy of what BrianTee sugested. Many thanks for his great work!

U27 is the µC controlling these functions. All external inputs are low-pass filtered and protected against miswiring. They are high-active, so either switch to +12V or +5V. Dedicated aux voltages are provided on the plugs. The Steer input is a digital input, Work is either digital (when using with Brian's software) or analog, so that it can be automatically controlled by the position sensor output of the hydraulic tool actuator (if available on the DIN 9684 plug). Current feedback for steering motors is provided on A0. The µC is also connected to the W5500 Ethernet interface. Mind, that either the Atmel or the ESP32 may use that option!

Mind that the µC runs on 3.3V while programming (see annotations @ Initial operation instructions).

The the Atmel µC is not used, you may leave these key parts out in order to safe costs: U27, X4, PRGBOOT, U22.

An ESP32 module U6 is mountable to provide dual-RTK, CAN and further interfacing functions. The one in the BOM has a connector for an external antenna, but the variant with the integrated antenna may also be used. The ESP can communicate to AgOpenGPS via USB, Ethernet or WiFi. The main function is handling dual-RTK-signals given by the two Ardusimple modules (when using one Ardusimple, no ESP is needed - can be connected directly to USB). In the future, two additional options are possible:

- all signals of the Atmel are also available to the ESP, so that the module may be used as single-µC-solution with an adapted firmware
- alternatively, the ESP may be used as UDP-to-serial bridge handling all UDP data and exchanging to steer, section control, IMU.

Only mount R31, R32, if ESP shall forward serial data to the (piggyback) section control unit.

Only mount R49, R50, if ESP shall forward serial data to the steer unit (Atmel).

For controlling the steering, there are two options: For Danfoss, only a level shifter (U800) is necessary. Do not mount U800, Q9, Q12 if this option is not used and the power stage is used instead.

That fully overload-protected motor/valve drivers are the ones of the IBT-2 (U9 and U10). It comes with separated 2-channel power lines at the power plug, so that a double-pole switch with positively opening contacts may be used for safe switch-off. This is especially mandatory for hydraulic steering. Furthermore, a DCDC converter may be used to generate 24V for driving the common Phidgets-Motor with increased dynamic. For 24V, choose a cap type with at least 25V (better: 35V) for C6, C7, C12, C13, C15 and C16! Q7 and Q8 provide a reverse polarity protection. No current is drawn on miswiring - just for the red LED. The bipolar small-signal transistors around the power stage provide a failsafe power decoupling between USB power for the logic and the power stage, so that any single failure in the power stage will not harm your tablet.

The two additional power switches U2 and U14 are only needed in case of an electric clutch (motor) or switching valve (hydraulic steering). The fifth pin of the power plug is used for that signal.

There is a current feedback for the µC, so that it can disengage autosteer at driver interference automatically. R28 is only needed the a digital switch-off signal with potentiometer adjustment is intended.

If no power stage is needed, do not place Q7, Q8, U9, U10, U2, U14, C6, C7, C12, C13, C15 and C16 to safe money.

Either the ESP or the Atmel may use the W5500 Ethernet chip exclusively. If not needed, do not mount U200, RJ200 and X1.

The switch-mode power supply around U250 is only needed for Ethernet- or Wifi-only use, when sourcing logic from USB is not possible. If not used, do not mount C250, L250, D251, R250..257.

The RS485 port (U8) is like what is also available with a cheap USB-RS485 stick based on a CH340 driver. 

# Placement overview

|if not needed...|...delete these key parts in BOM___.csv file|
|---|---|
|Atmel µC|U27, X4, PRGBOOT, U22|
|ESP32 module|U6, U5, U19|
|USB (normally needed for Arduino programming)|USBC1, U18, X2, USB2, U23, U5, U22, C28|
|Ethernet (cable)|U200, RJ200, X1|
|onboard IMU|U300, X300|
|Wheel angle sensor|U17|
|CAN|U19|
|Optoisolated digital output|U19|
|RS485|U8, C24=10R, C25=10R, R37, R38; do not mount: U8a, L1, L2, C24=100nF, C25=100nF, Q16|
|Power Line Communication|U8a, L1, L2, C24=100nF, C25=100nF, Q16; do not mount: U8, C24=10R, C25=10R, R37, R38|
|Danfoss|U800, Q9, Q12|
|motor/valve driver|Q7, Q8, U9, U10, U2, U14, C6, C7, C12, C13, C15, C16|
|power switch "enable"|U2, U14|
|connected to USB|U250, L250, D251, C250..257|

The 4 port USB hub connects the tablet/Notebook via either CN2 (PushIn) or CN8/CN13/TO_PC (USB-C) to the RTK-GNSS receiver and to the Nano or ESP32, the CANtact hardware, the RS-485 port or the internal 2 USB-A socket or the external USB-C socket. These alternatives are possible:

- USB1:  Arduino Nano Clone  

- USB2:  ESP32 - dual-RTK or single Ardusimple RTK board

- USB3:  Section control PCB addon

- USB4:    External 

All voltage and I/O functions are equipped with LEDs.

The PCB project was set up with the EDA program „EasyEDA“, which is freely usable. The Altium export has not been checked. 

Milling the aluminum housing, if using M8/M12 (see [drawings](mechanical_data)):
- let the CNC machine drill the 4 holes
- fix the cover with 4 screws M2.5x15
- mill the holes and the counterboring (tool: D=2mm, feed: 300mm/min, 12000RPM, advance: 2mm)
- repeat this step for the other cover

# Functional Safety Advice

Steering systems have to meet at least the agricultural performance level AgrPL d acc. UN ECE R79 (see professional systems like [this](https://www.mobil-elektronik.com/uploads/media/Prospekt_Brochure_ME_Agricultural_Vehicles_ENG.pdf))!

Especially with hydraulic control, the vehicle may likely get uncontrollable on a failure of the valve-controlling electronic which may result in fatal casualties or serious injuries!

For AgOpenGPS, the required safety level may be archieved by the fail-safe absense of power for the valve/motor controlling unit. This function must have at least the same safety/performance level.

The mandatory application for approval may base on the following arguments based on ISO 13849: 

- emergency-stop key meets IEC 60947-5-5/ISO 13850, in line with fuse meeting IEC60269-1 (both acc. to table D.3, ISO 13849-2)
- use of MELF type resistors for all 8.2kOhm resistors to meet table D.14, ISO 13849-2
- module is mounted inside a IP54 housing (acc. table D.5, ISO 13849-2)
- wiring acc. IEC 60204-1 (acc. table D.4, ISO 13849-2) 
- measure against tin whiskers are taken (acc. D.2.2, ISO 13849-2), e. g. use of 60/40 solder paste
- futhermore the software shall check the values of the signal „safesense“

(some ordering information underneath the German text)

# (German copy) Zusammenfassung

Dieses Projekt fasst alle Hardwarefunktionen, die zum Betrieb von AgOpenGPS notwendig sind, auf einem Board zusammen. Lediglich für Section Control kann eine weitere Leiterplatte hinzugefügt werden, die wahlweise aber auch im selben Gehäuse untergebracht werden kann. Ziel war es nicht, neue Hardwarefunktionen bereitzustellen, sondern eine robuste, monolitische, von professionellen Bestückern herstellbaren Einheit zu entwicklern, auf der der aktuelle Stand der Arduino-Firmware von BrianTee kann unverändert verwendet werden. Dieses Projekt ist der Nachfolger den Central-Unit 1.x, die nach wie vor für single-RTK-Anwendungen ohne Einschränkungen verwendet werden kann.

Es werden alle Steuerungsfunktionen für DC-Motoren und Hydraulikventile bereitgestellt, sowie die dafür notwendige Sensorik. Eine Anbindung ist über USB (beforzugt), Ethernet und WiFi möglich. Die Software von Brian und MTZ kann ohne Änderungen übernommen werden, wenn USB verwendet wird. 



Das [drawings/Structure_USB.png](Blockschaltbild) für USB zeigt links den mit dem Tablet verbundenen 4-fach USB-Hub, der folgende 4 Schnittstellen bereitstellt:

1. virtueller COM-Port für Atmel (Lenkung; entspricht der Funktionalität eines Arduino Nano)
2. RTK-GNSS zur Ortsbestimmung; entweder wird über USB direkt ein Ardusimple-Board angesprochen oder über einen virtuellen COM-Port ein ESP32 entsprechen dem Vorschlag von [AOG_Autosteer_ESP32](https://github.com/mtz8302/AOG_Autosteer_ESP32).
3. virtueller COM-Port für Section Control (wird auf einen Steckverbinder geführt für externes Section-Control-Modul (siehe Unterordner hier im Github)
4. eine USB-Buchse für allgemeine Verwendung (z. B. 5G-Stick, externen MEMS, etc)



Für [drawings/Structure_Ethernet_WiFi.png](Ethernet) muss der W5500 bestückt werden und die Software angepasst werden. Es ist dann sowohl eine single-µC-Lösung mit dem ESP32 als auch eine kombinierte ESP32/Atmel-Lösung möglich, bei der der ESP32 die Daten zentral verteilen muss. Zusätzlich muss das Schaltnetzteil bestückt werden, da ja die Logikspannung nun aus 12V erzeugt werden muss. Gleiches gilt für eine WLAN-Anbindung.



Durch die vielfältigen Optionen sieht das [drawings/Structure_all.png](Gesamtblockschaltbild) recht unübersichtlich aus. Es können aber alle Bauteile bestückt werden und zu einem späteren Zeitpunkt die genaue Topologie festgelegt werden. Z. B. wird durch Bestücken der USB-Buchse für einen Ardusimple automatisch der zugeordnete virtuelle COM-Port für dual-RTK deaktiviert.

Besonderer Wert wurde auf ein robustes Gehäuse und insbesondere robuste Steckverbinder und Kabel gelegt. Es sind M12/M8-Steckverbinder gerade oder abgewinkelt vorgesehen. Alternativ sind über auch steckbare PushIn-Steckverbinder bestückbar.

Folgende Funktionen sind vorgesehen:

- integrierte Arduino-Nano-Hardware
- ESP32 für dual-RTK
- ADC (ADS1115) für Lenkwinkelsensor
- Neigungssensor (BNO085/CMPS14)
- Motortreiber (H-Brücke wie IBT-2) mit zweikanaliger Abschaltung
- geschützte Digitaleingänge (als Konstantstromsenke)
- USB-Hub (4-port)
- CAN2.0 via ESP32
- virtueller serieller Port für RS485/ModbusRTU
- ganz viele Leuchtdioden

Folgende Anschlüsse sind vorgesehen:
- Stromversorgung 12V/24V (optional für Motor)
- USB-C zu Tablet/Notebook
- Lenkwinkelsensor
- Digitaleingänge
- I²C via M8 - Kabel zu IMU
- Lenkradmotor bzw. Hydraulikeinheit
- CAN2.0
- RS485/ModbusRTU
- Inkrementalgeber für Lenkradsensor
- USB-C 
- QWIIC für I²C-Kram

# Im Detail 

(wird fortlaufend ergänzt, allerdings meistens zunächst der englische Teil)

Der Arduino-Nano-Teil einschließlich der Neigungssensoren, des ADC und der Eingänge entspricht dem von BrianTee entwickelten Schaltplan. An dieser Stelle sei ihm für seine hervorragende Arbeit gedankt!

Eine ESP32-Leiterplatte ist alternativ bestückbar. In diesem Fall muss die Arduino-Software angepasst werden und der Nano dauerhaft im Reset-Zustand gehalten werden (Jumper auf 5, 6 von P1). Mit einem ESP32 steht dann hardwaremäßig auch ein CAN2.0 und ein RS485-Port zur Verfügung sowie Wifi und Bluetooth.

Der Motortreiber entspricht dem IBT-2. Er verfügt über eine getrennte, zweikanalig ausgeführte Stromversorgung am Spannungsversorgungsstecker, sodass hier ein geeigneter zweikanaliger zwangsöffnender Sicherheitsschalter angeschlossen werden kann. Insbesondere bei Hydraulikeinbindung ist dies zwingend. Auch kann so ein DC/DC-Wandler 12V > 24V vorgeschaltet werden, um eine höhere Lenkdynamik z. B. für den beliebten Phidgets-Motor zu erreichen.

Die 5. Leitung des Spannungsversorgungssteckers kann entweder mit einem geschützten Digitalausgang belegt werden (Jumper auf 1-2 von J8) oder für den Ein-Schalter verwendet werden (Jumper auf 2-3 von J8). Es wird keine Leistung geschaltet – ein kleiner Schalter reicht. Ein Schalter im Gehäuse wird an die 3-4 von J8 angeschlossen. Wird ein externer Leistungsschalter verwendet, müssen diese Kontakte mit einem Jumper überbrückt werden.

Die Digitaleingänge sind als Konstantstromsenke ausgeführt. Dadurch ist die Logik allerdings invertiert, also bitte Öffnerkontakte verwenden oder die Arduino-Firmware entsprechend anpassen.

Die Hardware des [CANtact-Projektes](https://cantact.io/cantact-pro/users-guide.html) auf Basis des Nexperia-µC LPC54616 ist optional bestückbar und stellt dann 2 CAN2.0-Schnittstellen zur Verfügung. Eine der beiden CAN2.0-Schnittstellen kann alternativ auch mit dem ESP32 angesteuert werden.

Die RS-485-Schnittstelle entspricht dem, was ein preiswerter USB-RS485-Stick auf Basis einen CH340 leistet. 

Alle Spannungen und I/O-Funktionen verfügen über Leuchtdioden.

Neben den I/O-Steckverbindern sollte mindestens P1 (Stiftleiste 2x5pol RM 2,54mm) bestückt werden, um die initiale Programmierung mit Hilfe eines Arduino Uno durchführen zu können. Notfalls können dort aber auch Kabel an- und nach erfolgter Programmierung wieder abgelötet werden. Je nach Einschaltoption wird noch J8 (Stiftleiste 1x4pol RM 2,54mm) und ein Jumper benötigt.

Das Leiterplattenprojekt wurde im frei verfügbaren EDA-Programm „EasyEDA“ erstellt. 

[Link zum EasyEDA-Projekt](https://easyeda.com/GoRoNb/aog_io-box)

Weitere allgemeine Informationen finden sich auch im übergeordneten Ordner.

Hilfestellung gibt es auch in der  [deutschsprachigen Nutzergruppe](t.me/AGOpenGPSGerman) und im [mehrsprachigen Forum](). 

Speziell zur Leiterplatteninbetriebnahme gibt es auch ein [Video](https://www.youtube.com/watch?v=w10TqOEIxdU).

# Erstinbetriebnahme
1. Ggf. fehlende SMD-Bauteile [nachbestücken](https://www.youtube.com/watch?v=dLczChhmDCY)
2. gewünschte Stiftleisten und Stecker auflöten
3. langsam die Spannung an CN4/POWER mit einer Strombegrenzung von 100mA hochregeln und gleichzeit die 5V-Spannung im Auge behalten (Eingangsstrom: 0mA bis ca. 4V, 20mA @ 4.5V, 12mA @ 12V; +5V darf nicht über 5,1V ansteigen!)
4. +3.3V überprüfen (sollte im Bereich 3.2..3.4V sein)
5. Arduino-Uno-Board mit P1 verbinden und Bootloader flashen (https://www.arduino.cc/en/Tutorial/BuiltInExamples/ArduinoISP) 
6. Uno-Board abstöpseln
7. über USB mit einem PC verbinden (entweder über CN2 oder CN13/CN8/USB-C): Der PC muss einen neuen Hub und mindestens eine neue serielle Schnittstelle anzeigen; bei mehrereren ist die des Arduino meistens die erste)
8. [BrianTee's Arduino-Code](https://github.com/farmerbriantee/AgOpenGPS/blob/master/Support_Files.zip) wie gewohnt mit der Arduino-Software flashen
9. Lenkwinkelsensor (auch als WAS oder LWS bezeichnet), Schalter, Motor anschliessen und mit AgOpenGPS testen

debugging: use terminal like HTerm and find out the correct COM port: connect to each possible one, set "DTR" and release "DTR". When releasing, the red LED blinks 3 times (bootloader). The green LED next to U3 will blink when sending any serial data to the Nano; this is also true when sending with the Arduino IDE (serial monitor)

Aktuell (2/2021) nicht bei JLCPCB bestückbar: U2, U10 (jeweils Lager leer), U11 (nicht bei LCSC verfügbar) und Steckverbinder (prinzipiell)

Fräsen des Alugehäuses, falls M8/M12 verwendet werden (siehe auch [Zeichnungen](mechanical_data)):
- mit der CNC-Maschine 4 Löcher bohren
- Seitenteil mit 4 Schrauben M2.5x15 dort befestigen
- Löcher und Senkung fräsen (Fräser: D=2mm, Vorschub: 300mm/min, 12000RPM, Zustellung: 2mm)
- Mit dem anderen Seitenteil die anderen Fräsdaten verwenden

# Hinweis zur Funktionalen Sicherheit

Fest verbaute Lenksystem, die z. B. in die Hydraulik eingreifen, müssen den Agricultural performance level AgrPL d nach UN ECE R79 (siehe z. B. professionelle Systeme wie [dieses](https://www.mobil-elektronik.com/uploads/media/Prospekt_Brochure_ME_Agrarfahrzeuge_DEU.pdf)) erfüllen!

Im Falle eines Ausfalls und dadurch ausgelösten Lenkbewegungen kann es zu tödlichen Unfällen oder schweren Verletzungen kommen!

Mit AgOpenGPS kann der notwendige Sicherheitslevel durch die fehlersichere Abschaltung der elektrischen Leistung für die Lenkaktoren erfolgen. Diese Abschaltung muss mindestens diesen Sicherheitslevel erfüllen.

Bei passender Installation mag eine Abnahme mag auf folgenden Argumenten basieren, die sich auf die EN-ISO 13849 stützen: 

- Schalter für die Stromversorgung der Lenkaktorik entspricht EN-IEC 60947-5-5/EN-ISO 13850, die Vorsicherung entspricht IEC60269-1 (beides entsprechend Tabelle D.3, EN-ISO 13849-2)
- die Leiterplatte enthält MELF-Widerstände (8.2kOhm), die Tabelle D.14, EN-ISO 13849-2 erfüllen (standardmäßig ist hier 1206 bestückt)
- die Leiterplatte ist in ein Gehäuse eingebaut, das mindestens IP54 erfüllt (Tabelle D.5, EN-ISO 13849-2)
- Die Verkabelung ist geschützt gemäß EN-IEC 60204-1 (Tabelle D.4, EN-ISO 13849-2) 
- Massnahmen gegen "tin whiskers" wurden getroffen, z. B. mit 60/40 Lötzinn gelötet (nach D.2.2, EN-ISO 13849-2)
- die Firmware sollte die Spannung des Signals „safesense“ messen und plausibilisieren

Alle Daten diese Repositories stehen unter der CERN Open-Hardware-Lizenz 1.2. Jede Haftung für Personenschäden und Sachschäden auf Grund Fehlern der Beschreibung oder Fehlern der Leiterplatte oder Software wird ausgeschlossen! 

# Component Sources (examples) / Beispiele Bezugsquellen:

M12/M8, general components:	    [Mouser](https://www.mouser.com/Connectors/Circular-Connectors/Circular-Metric-Connectors/_/N-76q5i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), [Reichelt](https://www.reichelt.de/de/en/sensor-actor-connectors-c7505.html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) - [Reichelt list](https://www.reichelt.de/my/1816987), [cable e. g.](https://catalog.weidmueller.com/catalog/Start.do?localeId=en&ObjectID=9457610150) 

(see [BOM-THT](production_data) for further information)

PushIn:		  Weidmueller [S2C-SMT 3.50/04/180G 3.5SN BK BX](https://catalog.weidmueller.com/catalog/Start.do?localeId=en&ObjectID=1290030000) + [B2CF 3.50/04/180 SN OR BX](https://catalog.weidmueller.com/catalog/Start.do?localeId=en&ObjectID=1277270000) via [Conrad](https://www.conrad.com)/[digikey](https://www.digikey.com)

(see [BOM-THT](production_data) for further information)

RTK receiver: 
- [Ardusimple](https://www.ardusimple.com/product/simplertk2b-basic-starter-kit-ip65/) (state-of-the-art receiver - mounting holes provided / Standardempfänger - Montagelöcher hierfür sind vorgesehen)

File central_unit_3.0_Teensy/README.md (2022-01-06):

# Central Unit V 3.0 AgOpenGPS/QtOpenGuidance  
(Informationen in deutscher Sprache unten)


This project includes all hardware function that are needed to run AgOpenGPS on one board. A 2nd board is only needed for Section Control, which can be placed inside the same housing. This setup uses the Teensy 4.1 board as control unit and is therefore not compatible with Brian's code. Nevertheless, there is software for Teensy (I'll add links later...)

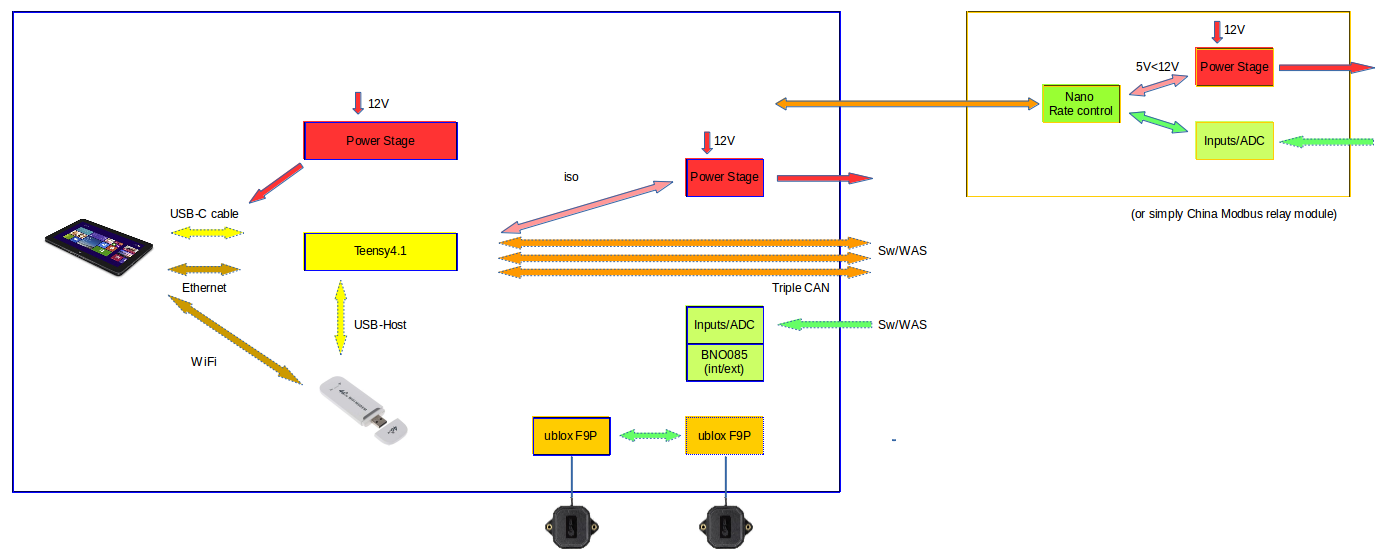
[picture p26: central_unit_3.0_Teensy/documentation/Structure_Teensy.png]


The [drawings/Structure_Teensy.png](full block diagram) is simple, because all controlling functions can be integrated inside the NXP controller, which is very powerfull. It would even be possible to run the complete AgOpenGPS on it and just provide a webbased interface for the tablet/mobile phone.

Functions' overview:

- I/Os needed for AOG
- connection to Ethernet
- USB host and device interfaces
- power supply
- motor driver incl. current feedback
- socket for one or two RTK units (Ardusimple)
- WAS input
- RS485 / Modbus
- 3 CAN

Special focus is given to the robust housing and industrial M12/M8 connetors (optional). PushIn connectors may also be used for single wire connections).




# 160 x 100 mm² 
2-layer 35µm, 1,6mm thickness, technology: 0.15mm/0.15mm/0.3mm; SMD assembly: 72 different parts, 252 parts overall, THT: only 2.54mm headers and plugs of your choice

[Link to EasyEDA project](https://easyeda.com/GoRoNb/agopengps-main-box_copy). The pick-and-place data in the [production data](production_data) is already rotated correctly for JLC.

# Functions in-cabin-unit for autosteering (all SMD + THT connectors)
- Teensy socket
- ADC (ADS1115) for wheel angle sensor (WAS)
- BNO085 option (as CMPS14 board)
- motor driver (H-bridge of IBT-2) with 2-channel switch-off
- current feedback from motor driver (may be used to quit autosteering on driver interaction)
- 2 protected digital inputs (WORK usable as analog input, too)
- one optional digital optoisolated output
- mounting holes for RKT unit board(s) (for dual-RTK); Ardusimple board has to be mounted slightly angular: distance between PCB and Ardusimple top: 10mm, antenna side: 16.5mm
- 3 CAN 
- many LEDs
- Ethernet/UDP option 
- WIFI option via Wifi-Stick

These [connections](Connections.pdf) are provided:
- Supply 12V/24V (optional for motor)
- USB-C to tablet/notebook
- Wheel angle sensor (WAS)
- Digital inputs
- USB for 5G stick for IMU
- Steering wheel motor / hydraulic unit
- CAN2.0
- RS485/ModbusRTU
- Incremental sensor for steering wheel
- USB-C
- QWIIC connector
- internal USB connectors
- RJ45 for Ethernet

# Initial Operation Instructions
1. if applicable: [assemble missing SMD parts](https://www.youtube.com/watch?v=dLczChhmDCY)
2. assemble alls THT parts: pin headers and connectors
3. slowly increase input voltage on CN4/POWER with current limit of 100mA while checking the 5V voltage (should be 0mA till about 4V, 20mA @ 4.5V, 12mA @ 12V; +5V must not rise up to more than 5.8V!)
4. check +3.3V (should be in the range 3.2..3.4V)
5. connect WAS, buttons, motor and do a test with AgOpenGPS

Some currents:
J3 closed:                                                 6mA@6V,   7mA@12V,   8mA@15V
J3 closed, with Teensy:                                  150mA@6V,  68mA@12V,  57mA@15V
J3 closed, with Teensy and two Ardusimple (max. power)): 335mA@6V, 160mA@12V, 137mA@15V

debugging: use terminal like HTerm and find out the correct COM port: connect to each possible one, set "DTR" and release "DTR". When releasing, the red LED blinks 3 times (bootloader). The green LED next to U3 will blink when sending any serial data to the Nano; this is also true when sending with the Arduino IDE (serial monitor)

Further information are also provided in the upper folder.

There is also an [English user group](t.me/agopengpsinternational) and a [multilingual forum](https://agopengps.discourse.group/t/smd-pcb-project-for-an-all-in-one-compact-pcb-for-aog-qog/3640). 

----------------------------------------------------------------------------------------------------------------------------

# Functional Description (to be continued..)

The part including roll sensor, ADC and digital inputs is a copy of what BrianTee sugested. Many thanks for his great work!

Dual-RTK and up to 3 CANs are provided. 

The motor driver is the one of the IBT-2. It comes with separated 2-channel power lines at the power plug, so that a double-pole switch with positively opening contacts may be used for safe switch-off. This is especially mandatory for hydraulic steering. Furthermore, a DCDC converter may be used to generate 24V for driving the common Phidgets-Motor with increased dynamic.

The fifth pin of the power plug may either be used for a protected digital output (jumper on 1-2 of J8) or as on-switching signal (jumper on 2-3 of J8). No high currents have to be switched – a small SPST switch is ok. A switch inside the housing would be connected to 3-4 of J8. If an external switch is used to cut of the supply directly, apply a jumper to 2-3 of J8.

All digital inputs are protected and made of constant current sinks. Therefore, the input is inverted, so that either NC pushbuttons may be used or the Arduino firmware may be modified.

All voltage and I/O functions are equipped with LEDs.

The PCB project was set up with the EDA program „EasyEDA“, which is freely usable. The Altium export has not been checked. 

Milling the aluminum housing, if using M8/M12 (see [drawings](mechanical_data)):
- let the CNC machine drill the 4 holes
- fix the cover with 4 screws M2.5x15
- mill the holes and the counterboring (tool: D=2mm, feed: 300mm/min, 12000RPM, advance: 2mm)
- repeat this step for the other cover

# Functional Safety Advice

Steering systems have to meet at least the agricultural performance level AgrPL d acc. UN ECE R79 (see professional systems like [this](https://www.mobil-elektronik.com/uploads/media/Prospekt_Brochure_ME_Agricultural_Vehicles_ENG.pdf))!

Especially with hydraulic control, the vehicle may likely get uncontrollable on a failure of the valve-controlling electronic which may result in fatal casualties or serious injuries!

For AgOpenGPS, the required safety level may be archieved by the fail-safe absense of power for the valve/motor controlling unit. This function must have at least the same safety/performance level.

The mandatory application for approval may base on the following arguments based on ISO 13849: 

- emergency-stop key meets IEC 60947-5-5/ISO 13850, in line with fuse meeting IEC60269-1 (both acc. to table D.3, ISO 13849-2)
- use of MELF type resistors for all 8.2kOhm resistors to meet table D.14, ISO 13849-2
- module is mounted inside a IP54 housing (acc. table D.5, ISO 13849-2)
- wiring acc. IEC 60204-1 (acc. table D.4, ISO 13849-2) 
- measure against tin whiskers are taken (acc. D.2.2, ISO 13849-2), e. g. use of 60/40 solder paste
- futhermore the software shall check the values of the signal „safesense“

(some ordering information underneath the German text)

# (German copy) Zusammenfassung

Dieses Projekt fasst alle Hardwarefunktionen, die zum Betrieb von AgOpenGPS notwendig sind, auf einem Board zusammen. Lediglich für Section Control kann eine weitere Leiterplatte hinzugefügt werden, die wahlweise aber auch im selben Gehäuse untergebracht werden kann. Ziel war es nicht, neue Hardwarefunktionen bereitzustellen, sondern eine robuste, monolitische, von professionellen Bestückern herstellbaren Einheit zu entwicklern. Es wird ein Teensy-µC-Board verwendet, das wesentlich leistungsfähiger als Arduino-Boards ist und alle notwendigen Funktionen aufnehmen kann bis hin zur vollständigen Integration von AgOpenGPS (in dem Fall würde das User-Interface als Website auf einem Tablet/Handy dargestellt). Das Board ist _nicht_ zu Brians Software kompatible. Die bestehenden Teensy-Implementierungen muss ich noch verlinken.

Es werden alle Steuerungsfunktionen für DC-Motoren und Hydraulikventile bereitgestellt, sowie die dafür notwendige Sensorik. Eine Anbindung ist über USB (beforzugt), Ethernet und WiFi möglich. Die Software von Brian und MTZ kann ohne Änderungen übernommen werden, wenn USB verwendet wird. 



Durch den Einsatz des Teensy als zentralen µC ergibt sich eine einfache Struktur. 

Besonderer Wert wurde auf ein robustes Gehäuse und insbesondere robuste Steckverbinder und Kabel gelegt. Es sind M12/M8-Steckverbinder gerade oder abgewinkelt vorgesehen. Alternativ sind über auch steckbare PushIn-Steckverbinder bestückbar.

Folgende Funktionen sind vorgesehen:

- Teensy-Steckplatz
- Steckplätze für (dual-)RTK
- ADC (ADS1115) für Lenkwinkelsensor
- Neigungssensor (BNO085/CMPS14)
- Motortreiber (H-Brücke wie IBT-2) mit zweikanaliger Abschaltung
- geschützte Digitaleingänge (als Konstantstromsenke)
- CAN2.0 (max 3 Schnittstellen)
- RS485/ModbusRTU
- ganz viele Leuchtdioden

Folgende Anschlüsse sind vorgesehen:
- Stromversorgung 12V/24V (optional für Motor)
- USB-C zu Tablet/Notebook
- Lenkwinkelsensor
- Digitaleingänge
- I²C via M8 - Kabel zu IMU
- Lenkradmotor bzw. Hydraulikeinheit
- CAN2.0
- RS485/ModbusRTU
- Inkrementalgeber für Lenkradsensor
- USB-C 
- QWIIC für I²C-Kram

# Im Detail 

(wird fortlaufend ergänzt, allerdings meistens zunächst der englische Teil)

Der Motortreiber entspricht dem IBT-2. Er verfügt über eine getrennte, zweikanalig ausgeführte Stromversorgung am Spannungsversorgungsstecker, sodass hier ein geeigneter zweikanaliger zwangsöffnender Sicherheitsschalter angeschlossen werden kann. Insbesondere bei Hydraulikeinbindung ist dies zwingend. Auch kann so ein DC/DC-Wandler 12V > 24V vorgeschaltet werden, um eine höhere Lenkdynamik z. B. für den beliebten Phidgets-Motor zu erreichen.

Die 5. Leitung des Spannungsversorgungssteckers kann entweder mit einem geschützten Digitalausgang belegt werden (Jumper auf 1-2 von J8) oder für den Ein-Schalter verwendet werden (Jumper auf 2-3 von J8). Es wird keine Leistung geschaltet – ein kleiner Schalter reicht. Ein Schalter im Gehäuse wird an die 3-4 von J8 angeschlossen. Wird ein externer Leistungsschalter verwendet, müssen diese Kontakte mit einem Jumper überbrückt werden.

Die Digitaleingänge sind als Konstantstromsenke ausgeführt. Dadurch ist die Logik allerdings invertiert, also bitte Öffnerkontakte verwenden oder die Arduino-Firmware entsprechend anpassen.

Alle Spannungen und I/O-Funktionen verfügen über Leuchtdioden.

Neben den I/O-Steckverbindern sollte mindestens P1 (Stiftleiste 2x5pol RM 2,54mm) bestückt werden, um die initiale Programmierung mit Hilfe eines Arduino Uno durchführen zu können. Notfalls können dort aber auch Kabel an- und nach erfolgter Programmierung wieder abgelötet werden. Je nach Einschaltoption wird noch J8 (Stiftleiste 1x4pol RM 2,54mm) und ein Jumper benötigt.

Das Leiterplattenprojekt wurde im frei verfügbaren EDA-Programm „EasyEDA“ erstellt.

[Link zum EasyEDA-Projekt](https://easyeda.com/GoRoNb/agopengps-main-box_copy).

Weitere allgemeine Informationen finden sich auch im übergeordneten Ordner.

Hilfestellung gibt es auch in der  [deutschsprachigen Nutzergruppe](t.me/AGOpenGPSGerman) und im [mehrsprachigen Forum](). 

Speziell zur Leiterplatteninbetriebnahme gibt es auch ein [Video](https://www.youtube.com/watch?v=w10TqOEIxdU).

# Erstinbetriebnahme
1. Ggf. fehlende SMD-Bauteile [nachbestücken](https://www.youtube.com/watch?v=dLczChhmDCY)
2. gewünschte Stiftleisten und Stecker auflöten
3. langsam die Spannung an CN4/POWER mit einer Strombegrenzung von 100mA hochregeln und gleichzeit die 5V-Spannung im Auge behalten (Eingangsstrom: 0mA bis ca. 4V, 20mA @ 4.5V, 12mA @ 12V; +5V darf nicht über 5,1V ansteigen!)
4. +3.3V überprüfen (sollte im Bereich 3.2..3.4V sein)
5. Lenkwinkelsensor (auch als WAS oder LWS bezeichnet), Schalter, Motor anschliessen und mit AgOpenGPS testen

debugging: use terminal like HTerm and find out the correct COM port: connect to each possible one, set "DTR" and release "DTR". When releasing, the red LED blinks 3 times (bootloader). The green LED next to U3 will blink when sending any serial data to the Nano; this is also true when sending with the Arduino IDE (serial monitor)

Aktuell (2/2021) nicht bei JLCPCB bestückbar: U2, U10 (jeweils Lager leer), U11 (nicht bei LCSC verfügbar) und Steckverbinder (prinzipiell)

Fräsen des Alugehäuses, falls M8/M12 verwendet werden (siehe auch [Zeichnungen](mechanical_data)):
- mit der CNC-Maschine 4 Löcher bohren
- Seitenteil mit 4 Schrauben M2.5x15 dort befestigen
- Löcher und Senkung fräsen (Fräser: D=2mm, Vorschub: 300mm/min, 12000RPM, Zustellung: 2mm)
- Mit dem anderen Seitenteil die anderen Fräsdaten verwenden

# Hinweis zur Funktionalen Sicherheit

Fest verbaute Lenksystem, die z. B. in die Hydraulik eingreifen, müssen den Agricultural performance level AgrPL d nach UN ECE R79 (siehe z. B. professionelle Systeme wie [dieses](https://www.mobil-elektronik.com/uploads/media/Prospekt_Brochure_ME_Agrarfahrzeuge_DEU.pdf)) erfüllen!

Im Falle eines Ausfalls und dadurch ausgelösten Lenkbewegungen kann es zu tödlichen Unfällen oder schweren Verletzungen kommen!

Mit AgOpenGPS kann der notwendige Sicherheitslevel durch die fehlersichere Abschaltung der elektrischen Leistung für die Lenkaktoren erfolgen. Diese Abschaltung muss mindestens diesen Sicherheitslevel erfüllen.

Bei passender Installation mag eine Abnahme mag auf folgenden Argumenten basieren, die sich auf die EN-ISO 13849 stützen: 

- Schalter für die Stromversorgung der Lenkaktorik entspricht EN-IEC 60947-5-5/EN-ISO 13850, die Vorsicherung entspricht IEC60269-1 (beides entsprechend Tabelle D.3, EN-ISO 13849-2)
- die Leiterplatte enthält MELF-Widerstände (8.2kOhm), die Tabelle D.14, EN-ISO 13849-2 erfüllen (standardmäßig ist hier 1206 bestückt)
- die Leiterplatte ist in ein Gehäuse eingebaut, das mindestens IP54 erfüllt (Tabelle D.5, EN-ISO 13849-2)
- Die Verkabelung ist geschützt gemäß EN-IEC 60204-1 (Tabelle D.4, EN-ISO 13849-2) 
- Massnahmen gegen "tin whiskers" wurden getroffen, z. B. mit 60/40 Lötzinn gelötet (nach D.2.2, EN-ISO 13849-2)
- die Firmware sollte die Spannung des Signals „safesense“ messen und plausibilisieren

Alle Daten diese Repositories stehen unter der CERN Open-Hardware-Lizenz 1.2. Jede Haftung für Personenschäden und Sachschäden auf Grund Fehlern der Beschreibung oder Fehlern der Leiterplatte oder Software wird ausgeschlossen! 

# Component Sources (examples) / Beispiele Bezugsquellen:

M12/M8, general components:	    [Mouser](https://www.mouser.com/Connectors/Circular-Connectors/Circular-Metric-Connectors/_/N-76q5i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), [Reichelt](https://www.reichelt.de/de/en/sensor-actor-connectors-c7505.html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) - [Reichelt list](https://www.reichelt.de/my/1816987), [cable e. g.](https://catalog.weidmueller.com/catalog/Start.do?localeId=en&ObjectID=9457610150) 

(see [BOM-THT](production_data) for further information)

PushIn:		  Weidmueller [S2C-SMT 3.50/04/180G 3.5SN BK BX](https://catalog.weidmueller.com/catalog/Start.do?localeId=en&ObjectID=1290030000) + [B2CF 3.50/04/180 SN OR BX](https://catalog.weidmueller.com/catalog/Start.do?localeId=en&ObjectID=1277270000) via [Conrad](https://www.conrad.com)/[digikey](https://www.digikey.com)

(see [BOM-THT](production_data) for further information)

RTK receiver: 
- [Ardusimple](https://www.ardusimple.com/product/simplertk2b-basic-starter-kit-ip65/) (state-of-the-art receiver - mounting holes provided / Standardempfänger - Montagelöcher hierfür sind vorgesehen)

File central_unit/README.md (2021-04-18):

# Central Unit AgOpenGPS/QtOpenGuidance  
(Informationen in deutscher Sprache unten)

Tested yet:
- USB hub, USB devices, USB-C 
- Atmel section with I/Os needed for AOG
- connection to Ethernet
- power supply
- motor driver incl. current feedback
- WAS input
- RS485 / Modbus

Still untested:
- CAN
- ESP32 option
- Bynav option

Not working:
- USB-C PD and data in parallel

This setup does not include new functions but provides a robust, monolitic unit that may be manufactured by professionel EMS providers. The central unit is compatible to [BrianTee‘s Nano firmware](https://github.com/farmerbriantee/AgOpenGPS/blob/master/Support_Files.zip) and to my [improved version](code/Autosteer_USB_CMPS14_low_jitter_twistable/). If the ESP32 option is used, download [AOG_Autosteer_ESP32](https://github.com/mtz8302/AOG_Autosteer_ESP32).

Special focus is given to the robust housing and industrial M12/M8 connetors (optional). PushIn connectors may also be used for single wire connections).

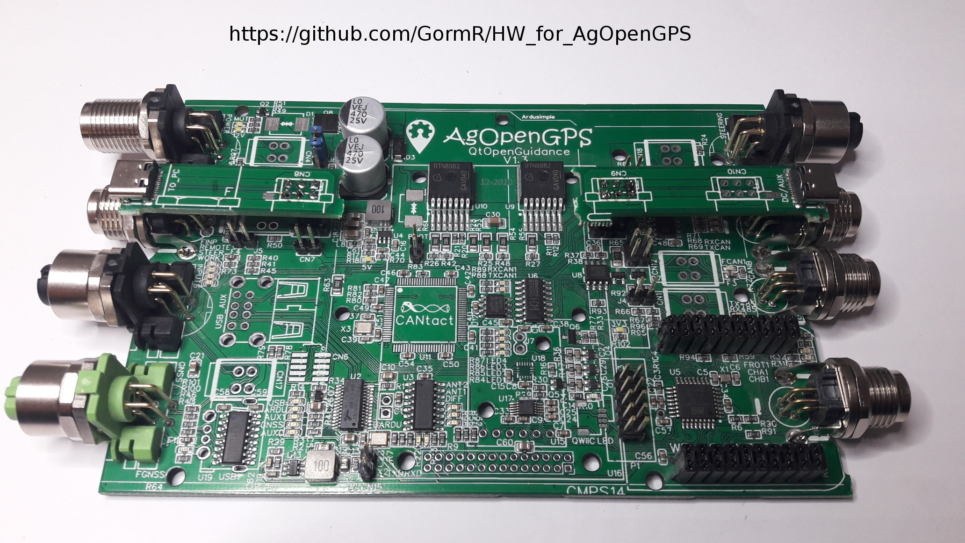
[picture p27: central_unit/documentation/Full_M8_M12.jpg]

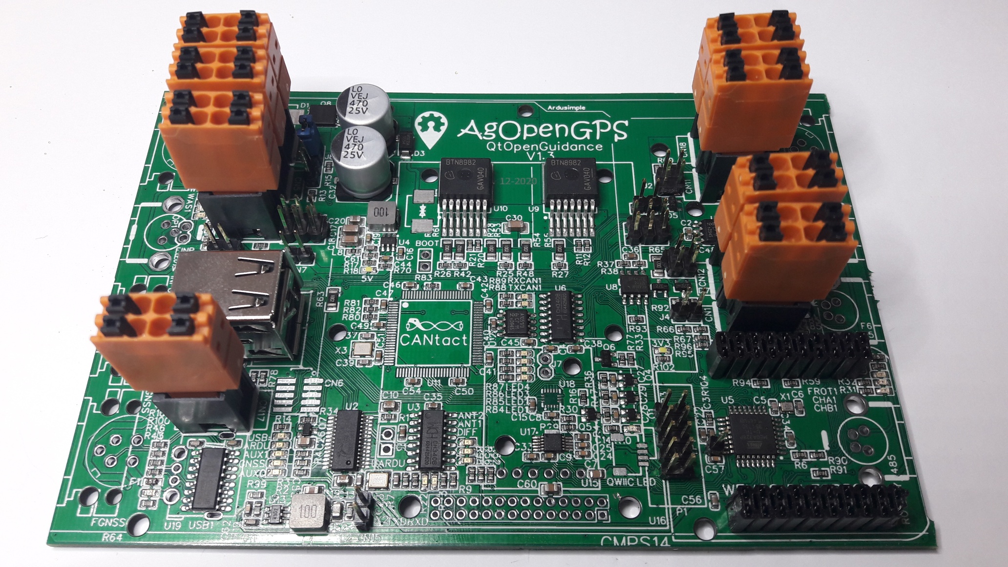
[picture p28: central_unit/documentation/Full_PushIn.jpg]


# 150 x 92 mm² 
2-layer 35µm, 1,6mm thickness, technology: 0.15mm/0.15mm/0.3mm; SMD assembly: 72 different parts, 252 parts overall, THT: only 2.54mm headers and plugs of your choice

[Link to EasyEDA project](https://oshwlab.com/GoRoNb/agopengps-main-box). The pick-and-place data in the [production data](production_data) is already rotated correctly for JLC.

# Functions in-cabin-unit for autosteering (all SMD + THT connectors)
- integrated Arduino-Nano hardware
- option for ESP32-Module (Arduino Firmware has to be adapted)
- ADC (ADS1115) for wheel angle sensor (WAS)
- roll sensor (MMA8452)
- BNO085 option (as CMPS14 board)
- motor driver (H-bridge of IBT-2) with 2-channel switch-off
- current feedback from motor driver (may be used to quit autosteering on driver interaction)
- 3 protected digital inputs (2oo3 usable as analog inputs on ESP32)
- one optional digital protected 12V output
- mounting holes for Ardusimple board(s)
- connector for Bynav-C1 board
- mounting holes for rooftop unit board (for dual-RTK)
- USB hub (4-port)
- USB and power supply for tablet/notebook via one USB-C (external DC adapter needed)
- integrated CANtact hardware (2x CAN2.0)
- virtual serial port for RS485/ModbusRTU
- many LEDs
- Ethernet/UDP option 

These [connections](Connections.pdf) are provided:
- Supply 12V/24V (optional for motor)
- USB-C to tablet/notebook
- Wheel angle sensor (WAS)
- Digital inputs
- USB via M12-D cable to RTK-GNSS unit
- Steering wheel motor / hydraulic unit
- 2x CAN2.0
- RS485/ModbusRTU
- Incremental sensor for steering wheel
- 2x USB-C (tablet + DC converter/Aux)
- Pixhawk connector (to Ardusimple, RS232 converter or any I²C/serial equipment)
- QWIIC connector
- internal USB connectors
- internal Bynav-C1 connector
- connector to [Ethernet shield](https://de.aliexpress.com/item/32548974618.html) - cut out "clkout" pin before connecting!!
- option to control a 6/2 valve (rename "xU14" to "U14" and delete R59, R76 and F7 in BOM; make a solder joint underneat CN18 to connect signal "+SERVO" to "-MOTOR").

# Initial Operation Instructions
1. if applicable: [assemble missing SMD parts](https://www.youtube.com/watch?v=dLczChhmDCY)
2. assemble alls THT parts: pin headers and connectors
3. connect 3-4 @ J8 (on)
4. slowly increase input voltage on CN4/POWER with current limit of 100mA while checking the 5V voltage (should be 0mA till about 4V, 20mA @ 4.5V, 12mA @ 12V; +5V must not rise up to more than 5.1V!)
5. check +3.3V (should be in the range 3.2..3.4V)
6. connect Arduino Uno board and flash bootloader via P1 (https://www.arduino.cc/en/Tutorial/BuiltInExamples/ArduinoISP) 
7. disconnect Uno board and connect USB (either CN2 or CN13/CN8/USB-C): The PC should display a new USB hub at least one several serial device 
8. flash [BrianTee's Arduino code](https://github.com/farmerbriantee/AgOpenGPS/blob/master/Support_Files.zip) via Arduino software
9. connect WAS, buttons, motor and do a test with AgOpenGPS

debugging: use terminal like HTerm and find out the correct COM port: connect to each possible one, set "DTR" and release "DTR". When releasing, the red LED blinks 3 times (bootloader). The green LED next to U3 will blink when sending any serial data to the Nano; this is also true when sending with the Arduino IDE (serial monitor)

Some functions are shown in [my English](https://www.youtube.com/watch?v=BdSSeIprusM) or [German video.](https://www.youtube.com/watch?v=w10TqOEIxdU).

Further information are also provided in the upper folder.

There is also an [English user group](t.me/agopengpsinternational) and a [multilingual forum](https://agopengps.discourse.group/t/smd-pcb-project-for-an-all-in-one-compact-pcb-for-aog-qog/3640). 

----------------------------------------------------------------------------------------------------------------------------

# Functional Description (to be continued..)

The Arduino part including roll sensor, ADC and digital inputs is a copy of what BrianTee sugested. Many thanks for his great work!

An ESP32 MINI module is mountable alternatively. In that case, the Arduino firmware has to be adapted and the Nano has to send to reset mode by using a jumper (pins 5+6 of P1).   With an ESP32, one CAN2.0 and the RS485 port is usable e. g. for external relay modules via ModbusRTU. Wifi and Bluetooth may also be used.

The motor driver is the one of the IBT-2. It comes with separated 2-channel power lines at the power plug, so that a double-pole switch with positively opening contacts may be used for safe switch-off. This is especially mandatory for hydraulic steering. Furthermore, a DCDC converter may be used to generate 24V for driving the common Phidgets-Motor with increased dynamic.

The fifth pin of the power plug may either be used for a protected digital output (jumper on 1-2 of J8) or as on-switching signal (jumper on 2-3 of J8). No high currents have to be switched – a small SPST switch is ok. A switch inside the housing would be connected to 3-4 of J8. If an external switch is used to cut of the supply directly, apply a jumper to 2-3 of J8.

All digital inputs are protected and made of constant current sinks. Therefore, the input is inverted, so that either NC pushbuttons may be used or the Arduino firmware may be modified.

The hardware of the CANtact project based on the Nexperia µC LPC54616 is optionally mountable and may provide two CAN2.0 ports under control of the tablet. One the two ports may alternativly driven by the ESP32.

The RS485 port is like what is also available with a cheap USB-RS485 stick based on a CH340 driver. 

The 4 port USB hub connects the tablet/Notebook via either CN2 (PushIn) or CN8/CN13/TO_PC (USB-C) to the RTK-GNSS receiver and to the Nano or ESP32, the CANtact hardware, the RS-485 port or the internal 2 USB-A socket or the external USB-C socket. These alternatives are possible:

- USB1:  Arduino Nano Clone  (XOR)   ESP32 (if U3 not mounted.)

- USB2:    RS485      (XOR)     Internal USB-A (if U5 not mounted) (XOR)     External USB-C (if U5 not mounted)

- USB3:    CANtact   (XOR)      Internal USB-A (e. g. for ESP32 parallel to Nano)

- USB4:    External RTK receiver via M12-D (if U19 not mounted) (XOR) Bynav-C1 board (XOR) internal USB (e. g. for Ardusimple via [USB cable](https://de.aliexpress.com/item/4000533815530.html) + [Antenna pigtail](https://de.aliexpress.com/item/4000245307369.html)):

Concerning USB4:

Option1: USB via M12-D: U19, R100, R101 not mounted

Option2: I²C via M12-D, serial device for RS232 - converter or Ardusimple @ ARDU1 or Bynav RTK receiver @ U16: R43, R46 not mounted

Option3: I²C via M12-D, additional internal USB (USB1): R43, R46, U19 not mounted

All voltage and I/O functions are equipped with LEDs.

Tablets with USB-C plug may be connected with a single USB-C wire for power and data, when a 12V USB-C DC converter is connected to the 2nd USB plug. Both USB-C plugs are mounted on a piggyback PCB on top of the M8 plugs.

The PCB project was set up with the EDA program „EasyEDA“, which is freely usable. The Altium export has not been checked. 

Milling the aluminum housing, if using M8/M12 (see [drawings](mechanical_data)):
- let the CNC machine drill the 4 holes
- fix the cover with 4 screws M2.5x15
- mill the holes and the counterboring (tool: D=2mm, feed: 300mm/min, 12000RPM, advance: 2mm)
- repeat this step for the other cover

# Functional Safety Advice

Steering systems have to meet at least the agricultural performance level AgrPL d acc. UN ECE R79 (see professional systems like [this](https://www.mobil-elektronik.com/uploads/media/Prospekt_Brochure_ME_Agricultural_Vehicles_ENG.pdf))!

Especially with hydraulic control, the vehicle may likely get uncontrollable on a failure of the valve-controlling electronic which may result in fatal casualties or serious injuries!

For AgOpenGPS, the required safety level may be archieved by the fail-safe absense of power for the valve/motor controlling unit. This function must have at least the same safety/performance level.

The mandatory application for approval may base on the following arguments based on ISO 13849: 

- emergency-stop key meets IEC 60947-5-5/ISO 13850, in line with fuse meeting IEC60269-1 (both acc. to table D.3, ISO 13849-2)
- use of MELF type resistors for all 8.2kOhm resistors to meet table D.14, ISO 13849-2
- module is mounted inside a IP54 housing (acc. table D.5, ISO 13849-2)
- wiring acc. IEC 60204-1 (acc. table D.4, ISO 13849-2) 
- measure against tin whiskers are taken (acc. D.2.2, ISO 13849-2), e. g. use of 60/40 solder paste
- futhermore the software shall check the values of the signal „safesense“

(some ordering information underneath the German text)

# (German copy) Zusammenfassung

Dieser Leiterplattenentwurf integriert mit Ausnahme des RTK-GNSS-Empfängers alle elektronischen Funktionen, die für einen automatische Lenkung der Projekte AgOpenGPS und QtOpenGuidance notwendig sind. So ist es möglich, auch die zweikanalige RTK-Einheit von Matthias (MTZ8302) zu verwenden. Ziel war es nicht, neue Hardwarefunktionen bereitzustellen, sondern eine robuste, monolitische, von professionellen Bestückern herstellbaren Einheit zu entwicklern, auf der der aktuelle Stand der Arduino-Firmware von BrianTee kann unverändert verwendet werden. 

Besonderer Wert wurde auf ein robustes Gehäuse und insbesondere robuste Steckverbinder und Kabel gelegt. Es sind M12/M8-Steckverbinder gerade oder abgewinkelt vorgesehen. Alternativ sind über auch steckbare PushIn-Steckverbinder bestückbar.

Folgende Funktionen sind vorgesehen:
- integrierte Arduino-Nano-Hardware
- Option für ESP32-Leiterplatte (Arduino-Firmware muss angepasst werden)
- ADC (ADS1115) für Lenkwinkelsensor
- Neigungssensor (MMA8452)
- Motortreiber (H-Brücke wie IBT-2) mit zweikanaliger Abschaltung
- geschützte Digitaleingänge (als Konstantstromsenke)
- USB-Hub (4-port)
- Spannungsversorgung auch für Tablet/Notebook via USB-C
- integrierte CANtact-Hardware (2x CAN2.0)
- virtueller serieller Port für RS485/ModbusRTU
- ganz viele Leuchtdioden

Folgende Anschlüsse sind vorgesehen:
- Stromversorgung 12V/24V (optional für Motor)
- USB-C zu Tablet/Notebook
- Lenkwinkelsensor
- Digitaleingänge
- USB via M12-D - Kabel zu RTK-GNSS-Einheit
- Lenkradmotor bzw. Hydraulikeinheit
- 2x CAN2.0
- RS485/ModbusRTU
- Inkrementalgeber für Lenkradsensor
- 2x USB-C (Tablet + DC-Wandler/Aux)
- Pixhawk als Alterantive zu USB für das Ardusimple-Board, aber auch für allgemeine I²C/serielle Anwendungen
- QWIIC für I²C-Kram

# Im Detail 

(wird fortlaufend ergänzt, allerdings meistens zunächst der englische Teil)

Der Arduino-Nano-Teil einschließlich der Neigungssensoren, des ADC und der Eingänge entspricht dem von BrianTee entwickelten Schaltplan. An dieser Stelle sei ihm für seine hervorragende Arbeit gedankt!

Eine ESP32-Leiterplatte ist alternativ bestückbar. In diesem Fall muss die Arduino-Software angepasst werden und der Nano dauerhaft im Reset-Zustand gehalten werden (Jumper auf 5, 6 von P1). Mit einem ESP32 steht dann hardwaremäßig auch ein CAN2.0 und ein RS485-Port zur Verfügung sowie Wifi und Bluetooth.

Der Motortreiber entspricht dem IBT-2. Er verfügt über eine getrennte, zweikanalig ausgeführte Stromversorgung am Spannungsversorgungsstecker, sodass hier ein geeigneter zweikanaliger zwangsöffnender Sicherheitsschalter angeschlossen werden kann. Insbesondere bei Hydraulikeinbindung ist dies zwingend. Auch kann so ein DC/DC-Wandler 12V > 24V vorgeschaltet werden, um eine höhere Lenkdynamik z. B. für den beliebten Phidgets-Motor zu erreichen.

Die 5. Leitung des Spannungsversorgungssteckers kann entweder mit einem geschützten Digitalausgang belegt werden (Jumper auf 1-2 von J8) oder für den Ein-Schalter verwendet werden (Jumper auf 2-3 von J8). Es wird keine Leistung geschaltet – ein kleiner Schalter reicht. Ein Schalter im Gehäuse wird an die 3-4 von J8 angeschlossen. Wird ein externer Leistungsschalter verwendet, müssen diese Kontakte mit einem Jumper überbrückt werden.

Die Digitaleingänge sind als Konstantstromsenke ausgeführt. Dadurch ist die Logik allerdings invertiert, also bitte Öffnerkontakte verwenden oder die Arduino-Firmware entsprechend anpassen.

Die Hardware des [CANtact-Projektes](https://cantact.io/cantact-pro/users-guide.html) auf Basis des Nexperia-µC LPC54616 ist optional bestückbar und stellt dann 2 CAN2.0-Schnittstellen zur Verfügung. Eine der beiden CAN2.0-Schnittstellen kann alternativ auch mit dem ESP32 angesteuert werden.

Die RS-485-Schnittstelle entspricht dem, was ein preiswerter USB-RS485-Stick auf Basis einen CH340 leistet. 

Der 4-Port-USB-Hub verbindet das Tablet/Notebook zum RTK-GNSS-Empfänger und wahlweise zum Nano bzw. ESP32, der CANtact-Hardware, der RS-485-Schnittstelle bzw. internen 2 USB-A-Buchsen einer externen USB-C-Buchse. Folgende Alternativen sind mit den 4 Ports möglich:

- USB1:  Arduino Nano Clone  (ODER)   ESP32 (wenn U3 nicht bestückt ist - ggf. auslöten mit Heißluft und Pinzette)

- USB2:    RS485      (ODER)     Interner USB-A (wenn U5 nicht bestückt ist) (ODER)     Externer USB-C (wenn U5 nicht bestückt ist)

- USB3:    CANtact   (ODER)      Interne USB-A (z. B. für ESP32 parallel zu Nano)

- USB4:    Externer RTK-Empfänger via M12-D (wenn U19 nicht bestückt ist) (ODER) Bynav-C1 Empfänger (ODER) interne USB (z. B. für Ardusimple via [USB cable](https://de.aliexpress.com/item/4000533815530.html) + [Antenna pigtail](https://de.aliexpress.com/item/4000245307369.html)):

Zu USB4:

Option1: USB via M12-D: U19, R100, R101 nicht bestücken/auslöten

Option2: I²C via M12-D, serieller Konverter für z. B. RS232 ODER Ardusimple @ ARDU1 (Pixhawk-Kabel) ODER Bynav RTK receiver @ U16: R43, R46 nicht bestücken/auslöten

Option3: I²C via M12-D, zusätzliche interne USB-A-Buchse (USB1): R43, R46, U19 nicht bestücken/auslöten

Alle Spannungen und I/O-Funktionen verfügen über Leuchtdioden.

Neben den I/O-Steckverbindern sollte mindestens P1 (Stiftleiste 2x5pol RM 2,54mm) bestückt werden, um die initiale Programmierung mit Hilfe eines Arduino Uno durchführen zu können. Notfalls können dort aber auch Kabel an- und nach erfolgter Programmierung wieder abgelötet werden. Je nach Einschaltoption wird noch J8 (Stiftleiste 1x4pol RM 2,54mm) und ein Jumper benötigt.

Tablets mit USB-C-Schnittstelle können mit einem einzigen Kabel für Daten und Stromversorgung angeschlossen werden, wenn ein 12V-USB-C-Ladeadapter an die zweite USB-C-Buchse angeschlossen wird. Die beiden USB-C-Buchsen sind auf Huckepack-Leiterplatten über den M8-Steckverbindern angeordnet.

Das Leiterplattenprojekt wurde im frei verfügbaren EDA-Programm „EasyEDA“ erstellt. Der Export nach Altium ist ungeprüft. 

Weitere allgemeine Informationen finden sich auch im übergeordneten Ordner.

Hilfestellung gibt es auch in der  [deutschsprachigen Nutzergruppe](t.me/AGOpenGPSGerman) und im [mehrsprachigen Forum](https://agopengps.discourse.group/t/smd-pcb-project-for-an-all-in-one-compact-pcb-for-aog-qog/3640). 

Speziell zur Leiterplatteninbetriebnahme gibt es auch ein [Video](https://www.youtube.com/watch?v=w10TqOEIxdU).

# Erstinbetriebnahme
1. Ggf. fehlende SMD-Bauteile [nachbestücken](https://www.youtube.com/watch?v=dLczChhmDCY)
2. gewünschte Stiftleisten und Stecker auflöten
3. Pins 3-4 @ J8 brücken (on)
4. langsam die Spannung an CN4/POWER mit einer Strombegrenzung von 100mA hochregeln und gleichzeit die 5V-Spannung im Auge behalten (Eingangsstrom: 0mA bis ca. 4V, 20mA @ 4.5V, 12mA @ 12V; +5V darf nicht über 5,1V ansteigen!)
5. +3.3V überprüfen (sollte im Bereich 3.2..3.4V sein)
6. Arduino-Uno-Board mit P1 verbinden und Bootloader flashen (https://www.arduino.cc/en/Tutorial/BuiltInExamples/ArduinoISP) 
7. Uno-Board abstöpseln
8. über USB mit einem PC verbinden (entweder über CN2 oder CN13/CN8/USB-C): Der PC muss einen neuen Hub und mindestens eine neue serielle Schnittstelle anzeigen; bei mehrereren ist die des Arduino meistens die erste)
9. [BrianTee's Arduino-Code](https://github.com/farmerbriantee/AgOpenGPS/blob/master/Support_Files.zip) wie gewohnt mit der Arduino-Software flashen
10. Lenkwinkelsensor (auch als WAS oder LWS bezeichnet), Schalter, Motor anschliessen und mit AgOpenGPS testen

debugging: use terminal like HTerm and find out the correct COM port: connect to each possible one, set "DTR" and release "DTR". When releasing, the red LED blinks 3 times (bootloader). The green LED next to U3 will blink when sending any serial data to the Nano; this is also true when sending with the Arduino IDE (serial monitor)

Aktuell (2/2021) nicht bei JLCPCB bestückbar: U2, U10 (jeweils Lager leer), U11 (nicht bei LCSC verfügbar) und Steckverbinder (prinzipiell)

Fräsen des Alugehäuses, falls M8/M12 verwendet werden (siehe auch [Zeichnungen](mechanical_data)):
- mit der CNC-Maschine 4 Löcher bohren
- Seitenteil mit 4 Schrauben M2.5x15 dort befestigen
- Löcher und Senkung fräsen (Fräser: D=2mm, Vorschub: 300mm/min, 12000RPM, Zustellung: 2mm)
- Mit dem anderen Seitenteil die anderen Fräsdaten verwenden

# Hinweis zur Funktionalen Sicherheit

Fest verbaute Lenksystem, die z. B. in die Hydraulik eingreifen, müssen den Agricultural performance level AgrPL d nach UN ECE R79 (siehe z. B. professionelle Systeme wie [dieses](https://www.mobil-elektronik.com/uploads/media/Prospekt_Brochure_ME_Agrarfahrzeuge_DEU.pdf)) erfüllen!

Im Falle eines Ausfalls und dadurch ausgelösten Lenkbewegungen kann es zu tödlichen Unfällen oder schweren Verletzungen kommen!

Mit AgOpenGPS kann der notwendige Sicherheitslevel durch die fehlersichere Abschaltung der elektrischen Leistung für die Lenkaktoren erfolgen. Diese Abschaltung muss mindestens diesen Sicherheitslevel erfüllen.

Bei passender Installation mag eine Abnahme mag auf folgenden Argumenten basieren, die sich auf die EN-ISO 13849 stützen: 

- Schalter für die Stromversorgung der Lenkaktorik entspricht EN-IEC 60947-5-5/EN-ISO 13850, die Vorsicherung entspricht IEC60269-1 (beides entsprechend Tabelle D.3, EN-ISO 13849-2)
- die Leiterplatte enthält MELF-Widerstände (8.2kOhm), die Tabelle D.14, EN-ISO 13849-2 erfüllen (standardmäßig ist hier 1206 bestückt)
- die Leiterplatte ist in ein Gehäuse eingebaut, das mindestens IP54 erfüllt (Tabelle D.5, EN-ISO 13849-2)
- Die Verkabelung ist geschützt gemäß EN-IEC 60204-1 (Tabelle D.4, EN-ISO 13849-2) 
- Massnahmen gegen "tin whiskers" wurden getroffen, z. B. mit 60/40 Lötzinn gelötet (nach D.2.2, EN-ISO 13849-2)
- die Firmware sollte die Spannung des Signals „safesense“ messen und plausibilisieren

Alle Daten diese Repositories stehen unter der CERN Open-Hardware-Lizenz 1.2. Jede Haftung für Personenschäden und Sachschäden auf Grund Fehlern der Beschreibung oder Fehlern der Leiterplatte oder Software wird ausgeschlossen! 

# Component Sources (examples) / Beispiele Bezugsquellen:

M12/M8, general components:	    [Mouser](https://www.mouser.com/Connectors/Circular-Connectors/Circular-Metric-Connectors/_/N-76q5i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), [Reichelt](https://www.reichelt.de/de/en/sensor-actor-connectors-c7505.html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) - [Reichelt list](https://www.reichelt.de/my/1816987), [cable e. g.](https://catalog.weidmueller.com/catalog/Start.do?localeId=en&ObjectID=9457610150) 

(see [BOM-THT](production_data) for further information)

PushIn:		  Weidmueller [S2C-SMT 3.50/04/180G 3.5SN BK BX](https://catalog.weidmueller.com/catalog/Start.do?localeId=en&ObjectID=1290030000) + [B2CF 3.50/04/180 SN OR BX](https://catalog.weidmueller.com/catalog/Start.do?localeId=en&ObjectID=1277270000) via [Conrad](https://www.conrad.com)/[digikey](https://www.digikey.com)

(see [BOM-THT](production_data) for further information)

ESP32 MINI:	[Aliexpress](https://de.aliexpress.com/wholesale?catId=0&SearchText=esp32+mini)

Housing for M8/M12 option: [Aliexpress](https://de.aliexpress.com/item/32967598546.html)

RTK receiver: 
- [Ardusimple](https://www.ardusimple.com/product/simplertk2b-basic-starter-kit-ip65/) (state-of-the-art receiver - mounting holes provided / Standardempfänger - Montagelöcher hierfür sind vorgesehen)
- [GNSS store](https://www.gnss.store/gnss-gps-modules/105-ublox-zed-f9p-rtk-gnss-receiver-board-with-sma-base-or-rover.html) (same type of receiver - especially for rooftop unit / gleicher Empfänger - gute Lösung für die Dacheinheit)
- [Bynav](https://www.bynav.com/en/products/gnss-boards/c1.html) (special software needed! / benötigt besondere Software!)

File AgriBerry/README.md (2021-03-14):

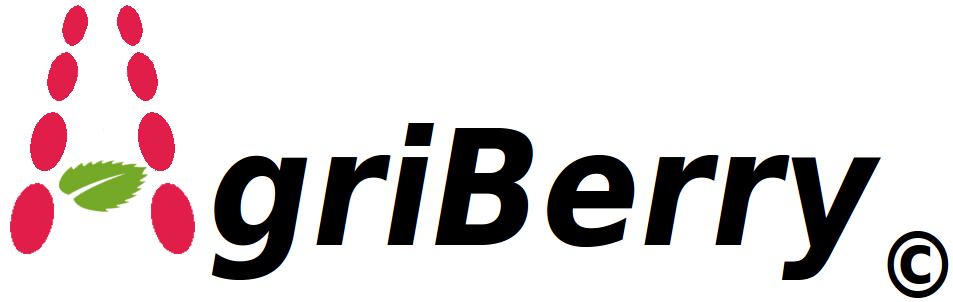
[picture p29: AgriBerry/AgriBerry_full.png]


# AgriBerry  
(Informationen in deutscher Sprache unten)

Pilot implementation of hardware for automatic steering of agricultural vehicles - Software missing yet!

Why copyright?
This project and its logo shall remain a free and public project. Although intended people selling professional service, the hard- and software shall always be free for the sake of everybody's information.

# Hardware features:
- analog and digital inputs
- motor/valve driver incl. aux. for 8/2
- Pi power supply from 14V nom.
- RS485(Modbus) e. g.for relay modules (section control, etc.)
- 2 CAN
- 4 GPDI + 2 GPDO
- Ardusimple board as piggyback
- made for HifiBerry plastic housing

The AgriBerry bases on BrianTee's great and altruistic [AgOpenGPS](https://github.com/farmerbriantee/AgOpenGPS) and transforms this onto a Raspberry Pi 4 base.

The user should benefit from the ease of simplicity:
- each component is available preassembled w/o the need of any SMD soldering
- software setup is as simple as putting an image to an SD card

It is designed as a robust, monolitic unit  that may be manufactured by professionel EMS providers. 

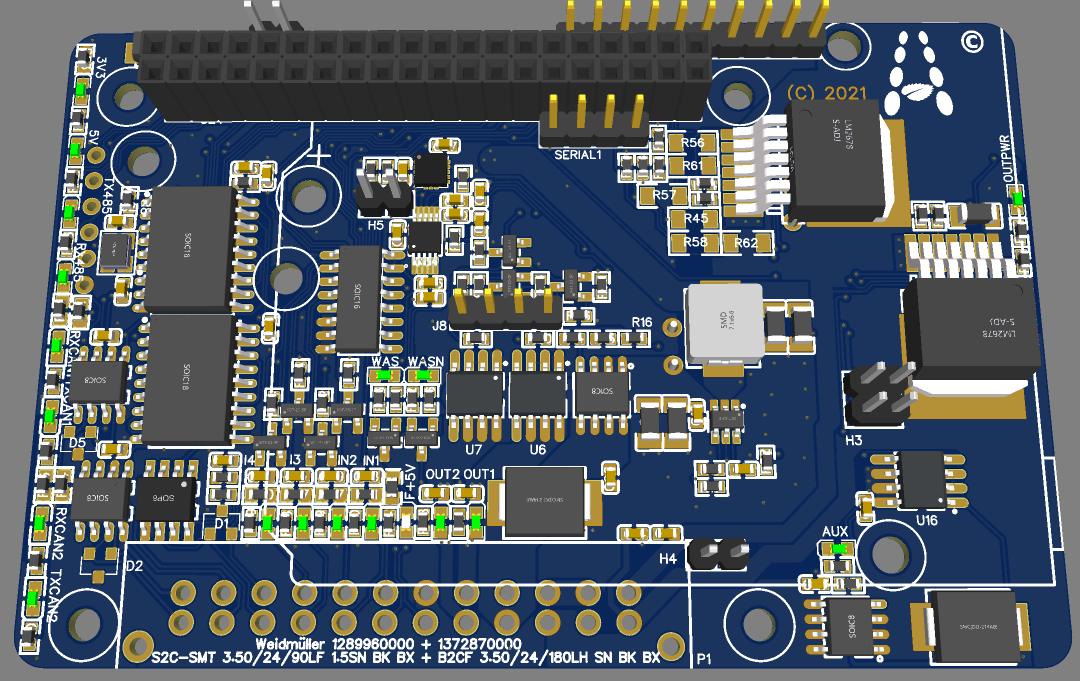
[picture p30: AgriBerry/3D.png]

(Annotation: The female connectors has to be mounted on the bottom side)

# 59.5 x 91 mm² 
2-layer 35µm, 1,6mm thickness, technology: 0.15mm/0.15mm/0.3mm; SMD assembly: about 70 different parts, 180 parts overall, THT: only 2.54mm connectors

[Link to EasyEDA project](https://oshwlab.com/GoRoNb/AgriNode). Estimated price of a single PCB assembly @ JLC: < $30, minimal version: < $20 @ a batch of 10 

Key electronical components:
- ADC: [ADS1115](https://www.ti.com/lit/gpn/ADS1113) - see [this project](https://learn.adafruit.com/raspberry-pi-analog-to-digital-converters/ads1015-slash-ads1115)
- IMU: [CMPS14](https://www.robotshop.com/en/tilt-compensated-magnetic-compass-cmps14.html) or [MMA8452](https://www.nxp.com/docs/en/data-sheet/MMA8452Q.pdf) - see [this project](https://robot-electronics.co.uk/htm/raspberry_pi_examples.htm), [this projekt](http://www.pibits.net/code/mma8452q-accelerometer-and-raspberry-pi-example.php) resp.
- CAN: [MCP2515](https://www.microchip.com/wwwproducts/en010406) - see [this project](https://vimtut0r.com/2017/01/17/can-bus-with-raspberry-pi-howtoquickstart-mcp2515-kernel-4-4-x/)

# Software architecture (suggestion)

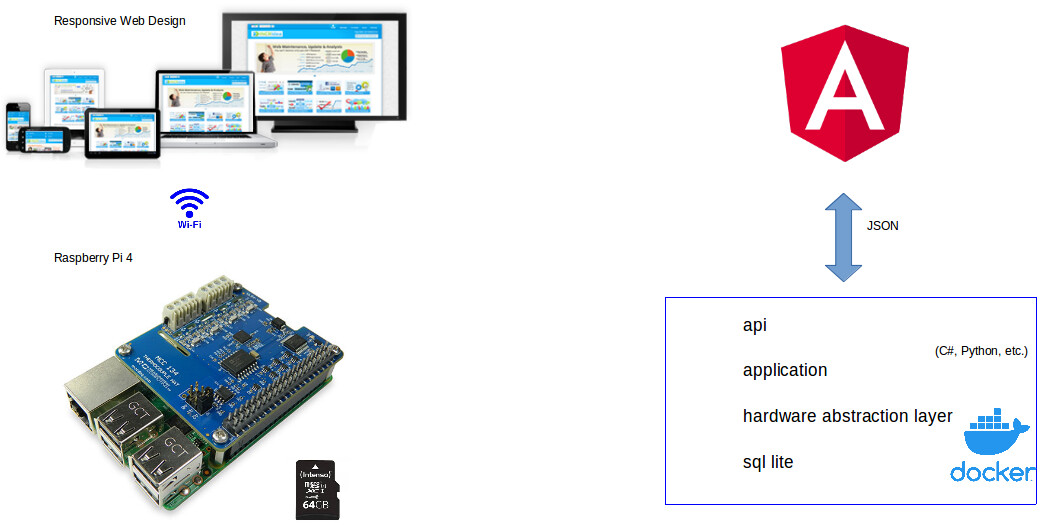
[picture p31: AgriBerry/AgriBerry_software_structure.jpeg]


# Initial Operation Instructions
1. if applicable: [assemble missing SMD parts](https://www.youtube.com/watch?v=dLczChhmDCY)
2. assemble all THT parts: pin headers and connectors
3. connect 3-4 @ J8 (on)
4. slowly increase input voltage on CN4/POWER with current limit of 100mA while checking the 5V voltage (should be 0mA till about 4V, 20mA @ 4.5V, 12mA @ 12V; +5V must not rise up to more than 5.1V!)
5. connect Raspberry PI 4 
8. insert micro-SD card with software image
9. connect WAS, buttons, motor and do a test 

There is also an [English user group](t.me/agopengpsinternational) and a [multilingual forum](https://agopengps.discourse.group/t/agriberry-hardware-draft/4357). 

----------------------------------------------------------------------------------------------------------------------------

# Functional Description (to be continued..)

The hardware including roll sensor, ADC and digital inputs is a following BrianTee's suggestion for AgOpenGPS. Many thanks for his great work!

The motor driver is the one of the IBT-2, but with genuine and automotive quality parts. It comes with separated 2-channel power lines at the power plug, so that a double-pole switch with positively opening contacts may be used for safe switch-off. This is especially mandatory for hydraulic steering. Furthermore, a DCDC converter may be used to generate 24V for driving the common Phidgets-Motor with increased dynamic. An auxilliary output for a 8/2 valve is provided.

All digital inputs are protected and both digital and analog readable.

All voltage and I/O functions are equipped with LEDs.

The PCB project was set up with the EDA program „EasyEDA“, which is freely usable. It is designed to fit into the HifiBerry plastic housing.

# Functional Safety Advice

Steering systems have to meet at least the agricultural performance level AgrPL d acc. UN ECE R79 (see professional systems like [this](https://www.mobil-elektronik.com/uploads/media/Prospekt_Brochure_ME_Agricultural_Vehicles_ENG.pdf))!

Especially with hydraulic control, the vehicle may likely get uncontrollable on a failure of the valve-controlling electronic which may result in fatal casualties or serious injuries!

For AgOpenGPS, the required safety level may be archieved by the fail-safe absense of power for the valve/motor controlling unit. This function must have at least the same safety/performance level.

The mandatory application for approval may base on the following arguments based on ISO 13849: 

- emergency-stop key meets IEC 60947-5-5/ISO 13850, in line with fuse meeting IEC60269-1 (both acc. to table D.3, ISO 13849-2)
- use of MELF type resistors for all 8.2kOhm resistors to meet table D.14, ISO 13849-2
- module is mounted inside a IP54 housing (acc. table D.5, ISO 13849-2)
- wiring acc. IEC 60204-1 (acc. table D.4, ISO 13849-2) 
- measure against tin whiskers are taken (acc. D.2.2, ISO 13849-2), e. g. use of 60/40 solder paste
- futhermore the software shall check the values of the signal „safesense“

(some ordering information underneath the German text)

# (German copy) Zusammenfassung

Dieser Leiterplattenentwurf integriert mit Ausnahme des RTK-GNSS-Empfängers alle elektronischen Funktionen, die für einen automatische Lenkung mit einem Raspberry PI 4 notwendig sind. Er orientiert sich an den Projekten AgOpenGPS und QtOpenGuidance. Ein Ardusimple kann aufgesteckt werden, aber es ist auch möglich, die zweikanalige RTK-Einheit von Matthias (MTZ8302) als externe Einheit zu verwenden. 

Besonderer Wert wurde ein industriell automatisch fertigbares kompaktes Design mit industriellen steckbaren PushIn-Steckverbindern gelegt.

# Hardwarefeatures:
- Ardusimple aufsteckbar
- analoge and digitale Eingänge
- Motor/Ventiltreiber incl. Hilfausgang für 8/2
- Pi Stromversorgung aus 14V nom.
- RS485(Modbus) z. B. für Relaismodule (section control, etc.)
- 2 CAN
- 4 GPDI + 2 GPDO
- Formfaktor for HifiBerry Kunststoffgehäuse

Das Leiterplattenprojekt wurde im frei verfügbaren EDA-Programm „EasyEDA“ erstellt.

Schlüsselkomponenten:
- ADC: [ADS1115](https://www.ti.com/lit/gpn/ADS1113) - z. B. [in diesem Projekt](https://learn.adafruit.com/raspberry-pi-analog-to-digital-converters/ads1015-slash-ads1115)
- IMU: [CMPS14](https://www.robotshop.com/en/tilt-compensated-magnetic-compass-cmps14.html) or [MMA8452](https://www.nxp.com/docs/en/data-sheet/MMA8452Q.pdf) - z. B. [in diesem Projekt](https://robot-electronics.co.uk/htm/raspberry_pi_examples.htm) bzw. [in diesem Projekt](http://www.pibits.net/code/mma8452q-accelerometer-and-raspberry-pi-example.php)
- CAN: [MCP2515](https://www.microchip.com/wwwproducts/en010406) - z. B. [in diesem Projekt](https://vimtut0r.com/2017/01/17/can-bus-with-raspberry-pi-howtoquickstart-mcp2515-kernel-4-4-x/)

Hilfestellung gibt es auch in der  [deutschsprachigen Nutzergruppe](t.me/AGOpenGPSGerman) und im [mehrsprachigen Forum](https://agopengps.discourse.group/t/agriberry-hardware-draft/4357). 

# Erstinbetriebnahme
1. Ggf. fehlende SMD-Bauteile [nachbestücken](https://www.youtube.com/watch?v=dLczChhmDCY)
2. gewünschte Stiftleisten und Stecker auflöten
3. Pins 3-4 @ J8 brücken (on)
4. langsam die Spannung an CN4/POWER mit einer Strombegrenzung von 100mA hochregeln und gleichzeit die 5V-Spannung im Auge behalten (Eingangsstrom: 0mA bis ca. 4V, 20mA @ 4.5V, 12mA @ 12V; +5V darf nicht über 5,1V ansteigen!)
5. Raspberry PI 4 anschliessen
6. Micro-SD-Karte mit Softwareimage einstecken
7. Lenkwinkelsensor (auch als WAS oder LWS bezeichnet), Schalter, Motor anschliessen und testen

# Hinweis zur Funktionalen Sicherheit

Fest verbaute Lenksystem, die z. B. in die Hydraulik eingreifen, müssen den Agricultural performance level AgrPL d nach UN ECE R79 (siehe z. B. professionelle Systeme wie [dieses](https://www.mobil-elektronik.com/uploads/media/Prospekt_Brochure_ME_Agrarfahrzeuge_DEU.pdf)) erfüllen!

Im Falle eines Ausfalls und dadurch ausgelösten Lenkbewegungen kann es zu tödlichen Unfällen oder schweren Verletzungen kommen!

Mit AgOpenGPS kann der notwendige Sicherheitslevel durch die fehlersichere Abschaltung der elektrischen Leistung für die Lenkaktoren erfolgen. Diese Abschaltung muss mindestens diesen Sicherheitslevel erfüllen.

Bei passender Installation mag eine Abnahme mag auf folgenden Argumenten basieren, die sich auf die EN-ISO 13849 stützen: 

- Schalter für die Stromversorgung der Lenkaktorik entspricht EN-IEC 60947-5-5/EN-ISO 13850, die Vorsicherung entspricht IEC60269-1 (beides entsprechend Tabelle D.3, EN-ISO 13849-2)
- die Leiterplatte enthält MELF-Widerstände (8.2kOhm), die Tabelle D.14, EN-ISO 13849-2 erfüllen (standardmäßig ist hier 1206 bestückt)
- die Leiterplatte ist in ein Gehäuse eingebaut, das mindestens IP54 erfüllt (Tabelle D.5, EN-ISO 13849-2)
- Die Verkabelung ist geschützt gemäß EN-IEC 60204-1 (Tabelle D.4, EN-ISO 13849-2) 
- Massnahmen gegen "tin whiskers" wurden getroffen, z. B. mit 60/40 Lötzinn gelötet (nach D.2.2, EN-ISO 13849-2)
- die Firmware sollte die Spannung des Signals „safesense“ messen und plausibilisieren

Alle Daten diese Repositories stehen unter der CERN Open-Hardware-Lizenz 1.2. Jede Haftung für Personenschäden und Sachschäden auf Grund Fehlern der Beschreibung oder Fehlern der Leiterplatte oder Software wird ausgeschlossen! 

# Component Sources (examples) / Beispiele Bezugsquellen:

PushIn:		  Weidmueller [S2C-SMT 3.50/24/90LF 1.5SN BK BX](https://catalog.weidmueller.com/catalog/Start.do?localeId=en&ObjectID=1289960000) + [B2CF 3.50/24/180LH SN BK BX](https://catalog.weidmueller.com/catalog/Start.do?localeId=en&ObjectID=1372870000) via [Conrad](https://www.conrad.com)/[digikey](https://www.digikey.com)

Housing: [HifiBerry](https://www.hifiberry.com/shop/cases/hifiberry-universal-case-black-pi4/)

RTK receiver: 
- [Ardusimple](https://www.ardusimple.com/product/simplertk2b-basic-starter-kit-ip65/) (state-of-the-art receiver - mounting holes provided / Standardempfänger - Montagelöcher hierfür sind vorgesehen)

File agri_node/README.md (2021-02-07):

# Universal ESP32-based node for agricultural/automotive use  
Status: Work in progress!

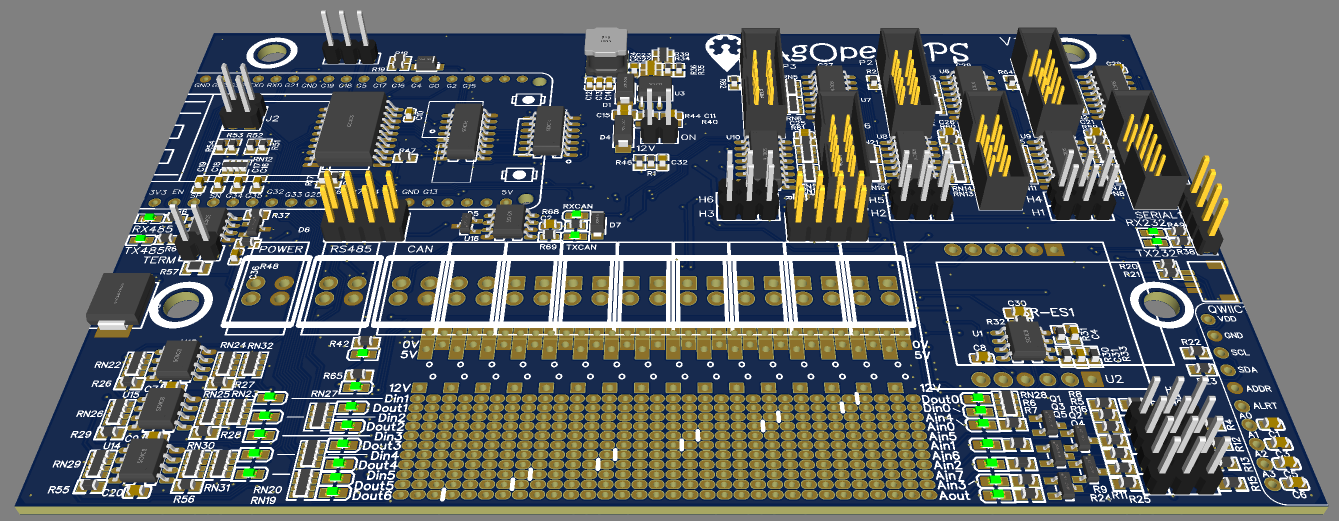
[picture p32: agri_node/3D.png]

[Project link](https://oshwlab.com/GoRoNb/generic_agri_node)

The AgriNode is designed as an inexpensive base board for an ESP32 module, optimized for agricultural/automotive use.

Apart from the connectors and modules, the board may be ordered completely SMD-assembled e. g. from JLCPCB for about US$80 for 10 PCBs (tax and shipping not included).

The following functions are provided:

- ESP32 module e. g. AZ-delivery (mind the pinning - unfortunately there is no standard!)

- Switch-mode power supply 6..20V

- 4x 16bit analog inputs Ain0..3, if ADS11145 module is mounted
   Input voltage range: 0..15V
   Impedance: voltage: 57kOhm, current: 150Ohm shunt to 0V

- 4x 12bit analog inputs Ain 4..7
   Input voltage range: 0..3.3V
   Impedance: 1MOhm

- 6x fast precise digital inputs: Din0..5 
    Input voltage range: 0..15V
    Threshold: 2.4V typ.
    Hytheresis: 0.3V typ.
    Impedance: 4.7kOhm

- 24x digital inputs: Din8..31 
    Input voltage range: 0..15V
    Input low, if input < 1.3V max.
    Input hight, if output > 4.5V min.
    Impedance: 4.7kOhm // 10kOhm clamping to 5V

- 6x fast digital outputs Dout1..6
    Output voltage 0V/5V
    Output impedance: 1kOhm

- 24x digital outputs Dout8..31
    Output voltage 0V/5V
    Output impedance: 1kOhm
    
- 1x output digital or analog DAC
    Output voltage 0V..12V
    Output impedance: 150Ohm

- 1x digital output Dout0
    Output voltage 0V/12V
    Output impedance: 150Ohm

Optional connectors:
- I/O with push-in (see picture underneath)
- I/O with 2.54mm pin headers (24 DI + 24 DO)
- QWIIC to further I²C devices
- 2x to IBT-2 module
- to RS-232 module
- CAN (driver already provided onboard)
- RS-485 (e. g. Modbus; driver already provided onboard)
- Ethernet/UDP w/ W5500 shield

The I/O area is user-defined by a matrix:

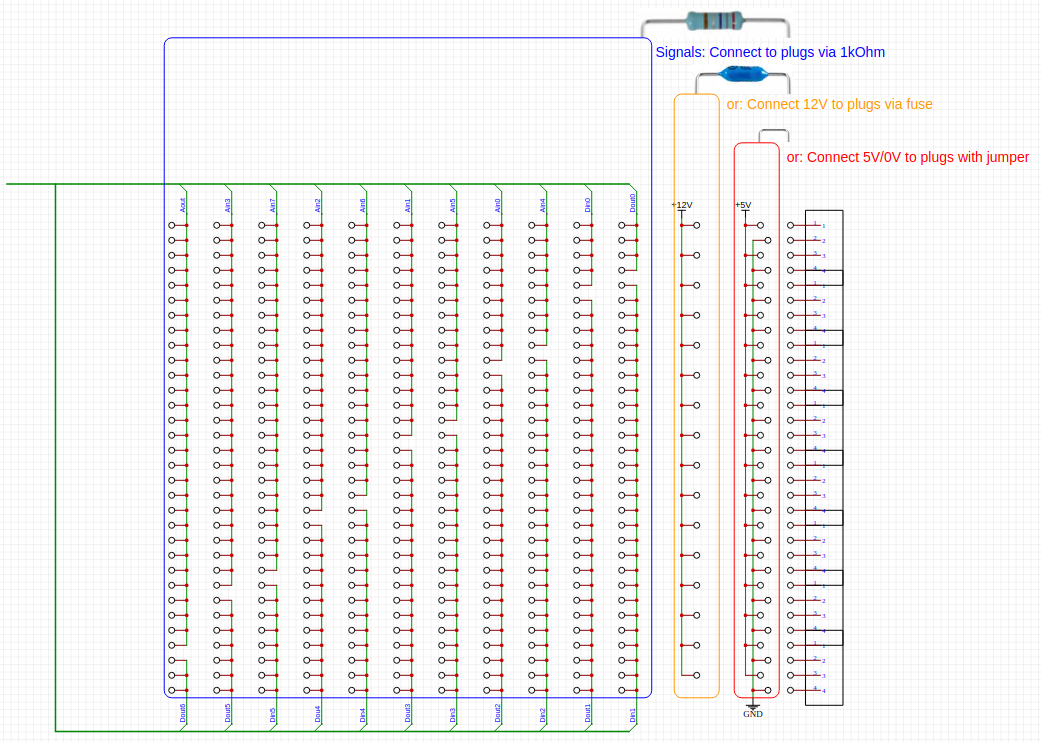
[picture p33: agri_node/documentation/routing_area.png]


Mind the [description of the connections](documentation/Schematic_Drawings_Node.pdf).

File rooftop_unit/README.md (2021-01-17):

# Autosteer and RTK units for AgOpenGPS/QtOpenGuidance  
Status: Draft - to be tested!

The dual RTK-GNSS receiver, based on an idea of MTZ8302.

This setup does not include new functions but provides a robust, monolitic unit  that may be manufactured by professionel EMS providers. The rooftop unit is similar to [MTZ8302's dual-RTK firmware](https://github.com/mtz8302/AOG_GPS_ESP32). 

Special focus is given to the robust housing and industrial M12/M8 connetors (optional). 

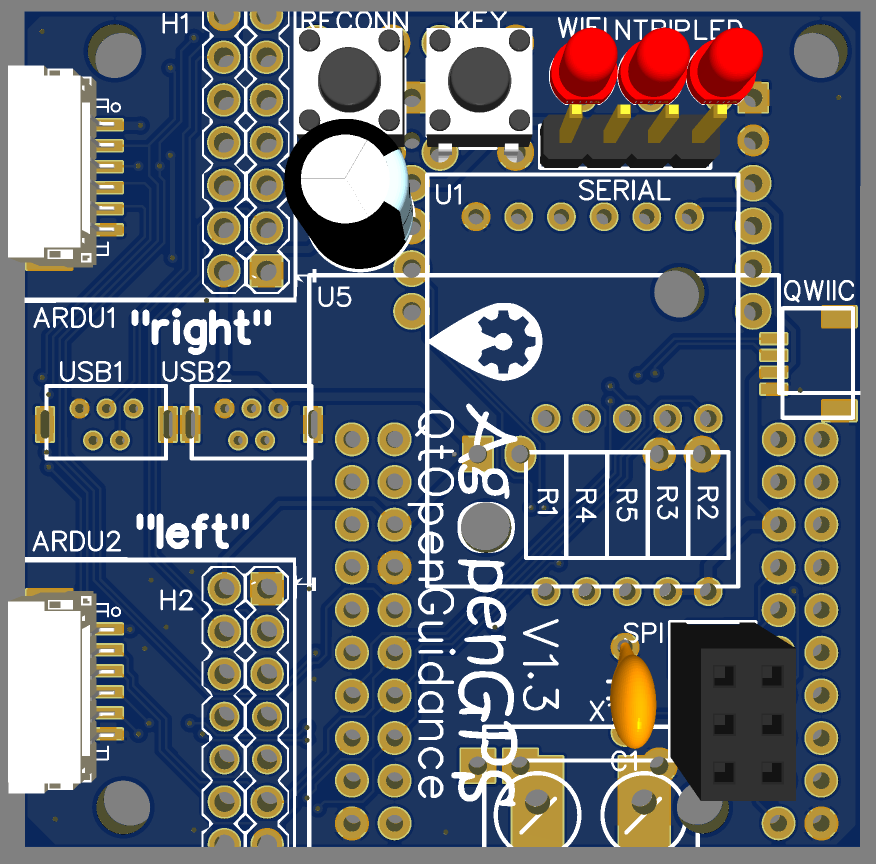
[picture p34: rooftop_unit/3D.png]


[Project link](https://easyeda.com/GoRoNb/autosteer-for-agopengps_copy_copy_copy_copy)
# Functions roof top unit for positioning (only THT):
- Dual RTK-GNSS receiver
- BNO085 option (as CMPS14 board)
- QWIIC connector
- based on ESP32 [Thx to MTZ8302](https://github.com/mtz8302/AOG_GPS_ESP32) and Jeep1945 (pinning taken from Jeep1945)
- RS232 output option for sprayer (NMEA string output or speed pulse)
- SPI connector for those who like to use an Ethernet shield
- 3 LEDs, 2 key inputs
- option for W5500 Ethernet board for UDP

The PCB project was set up with the EDA program „EasyEDA“, which is freely usable. The Altium export has not been checked. 

# (German copy) Zusammenfassung

Dieser Leiterplattenentwurf integriert mit Ausnahme des RTK-GNSS-Empfängers alle elektronischen Funktionen, die für einen automatische Lenkung der Projekte AgOpenGPS und QtOpenGuidance notwendig sind. So ist es möglich, auch die zweikanalige RTK-Einheit von Matthias (MTZ8302) zu verwenden. Ziel war es nicht, neue Hardwarefunktionen bereitzustellen, sondern eine robuste, monolitische, von professionellen Bestückern herstellbaren Einheit zu entwicklern, auf der der aktuelle Stand der Arduino-Firmware von BrianTee kann unverändert verwendet werden. 

Besonderer Wert wurde auf ein robustes Gehäuse und insbesondere robuste Steckverbinder und Kabel gelegt. Es sind M12/M8-Steckverbinder gerade oder abgewinkelt vorgesehen. Alternativ sind über auch steckbare PushIn-Steckverbinder bestückbar.

Das Leiterplattenprojekt wurde im frei verfügbaren EDA-Programm „EasyEDA“ erstellt. Der Export nach Altium ist ungeprüft. 

# Component Sources (examples):

M12/M8:	    [digikey](https://www.digikey.com), [Reichelt](https://www.reichelt.de/de/en/sensor-actor-connectors-c7505.html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)

ESP32 MINI:	[Aliexpress](https://de.aliexpress.com/wholesale?catId=0&SearchText=esp32+mini)

Housing Rooftop Unit: [Amazon](http://www.amazon.de/dp/B076KJZJN5/)

RTK receiver: [GNSS store](https://www.gnss.store/gnss-gps-modules/105-ublox-zed-f9p-rtk-gnss-receiver-board-with-sma-base-or-rover.html)

Ethernet: [W5500 board](https://de.aliexpress.com/item/32598945210.html)

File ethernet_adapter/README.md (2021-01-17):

# Ethernet/UDP shield for Central Unit  
Status: Draft - to be tested!

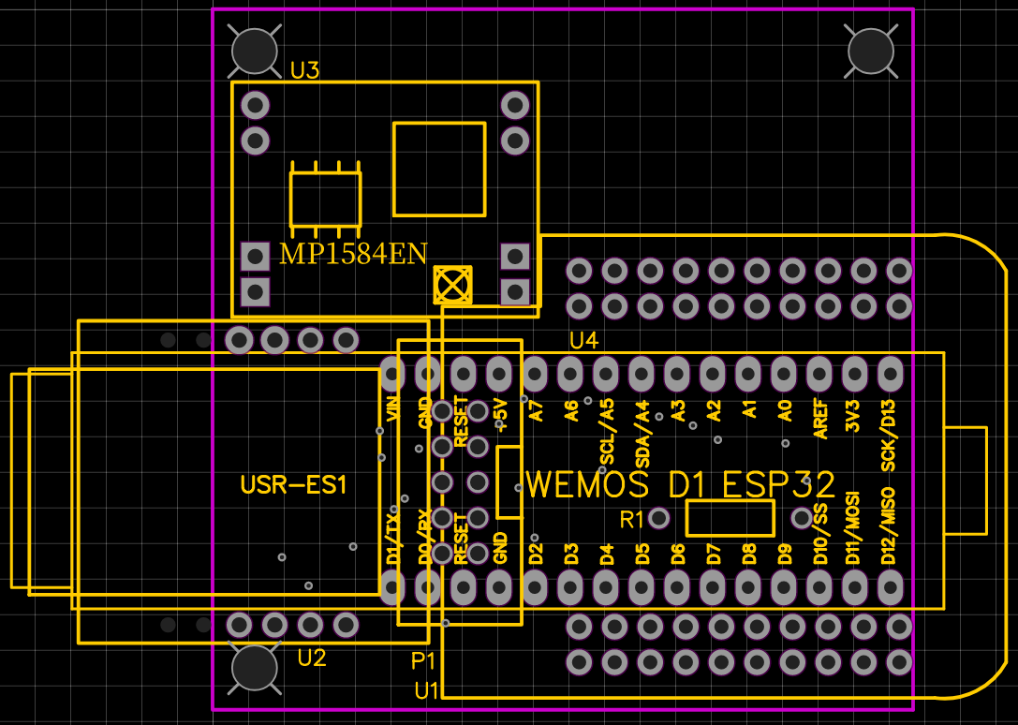
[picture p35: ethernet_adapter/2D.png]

[Project link](https://oshwlab.com/GoRoNb/ethernet-adapter-usr-es1-esp32)

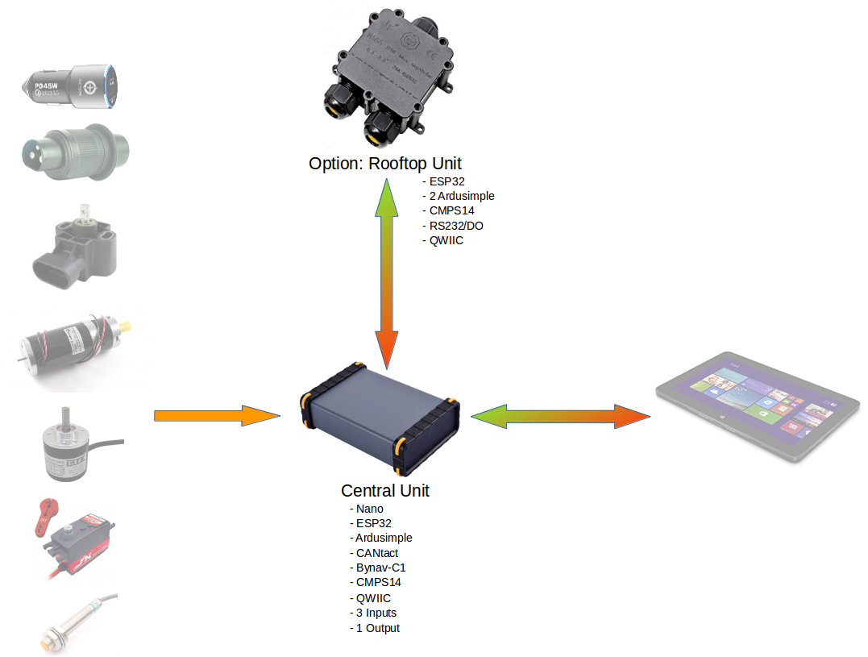
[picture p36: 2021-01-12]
Overview.png

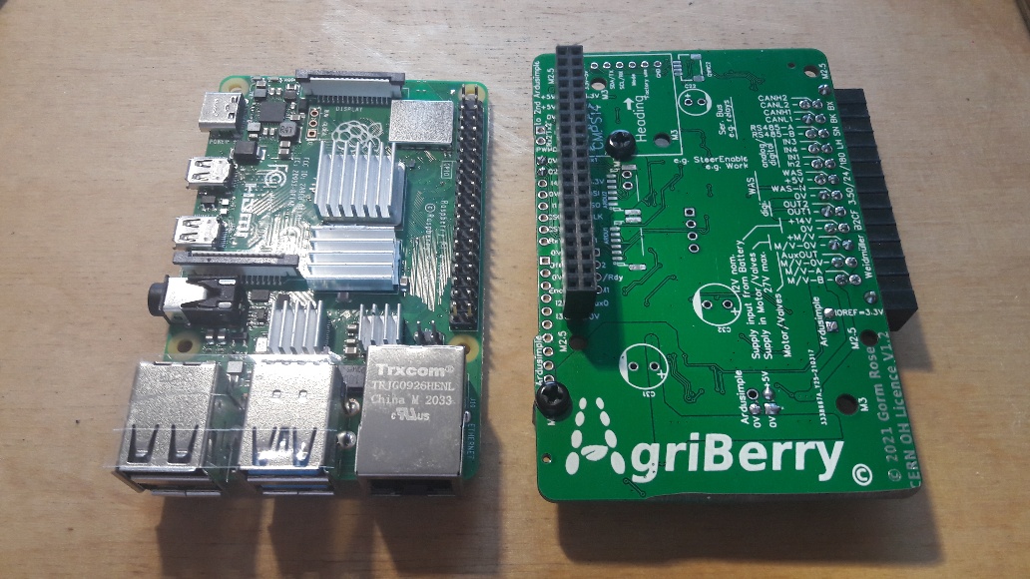
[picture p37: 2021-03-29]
AgriBerry/documentation/photos/20210329_185636_resized_1.jpg

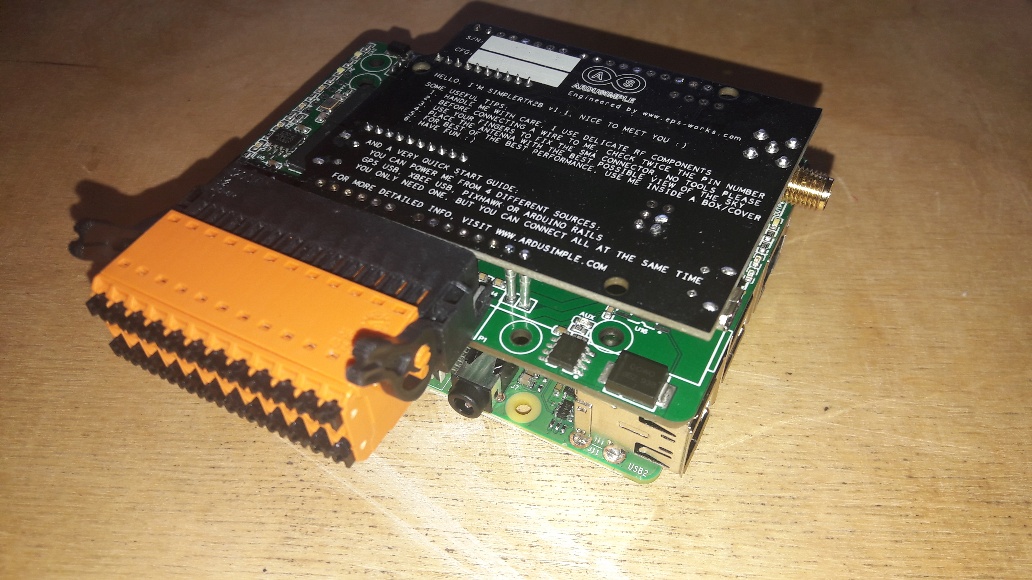
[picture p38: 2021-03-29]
AgriBerry/documentation/photos/20210329_185443_resized_1.jpg

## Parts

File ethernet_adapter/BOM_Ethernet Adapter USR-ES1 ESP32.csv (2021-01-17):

ID | Name | Designator | Footprint | Quantity | Manufacturer Part | Manufacturer | Supplier | Supplier Part | LCSC Assembly
1 | ENC28J60_NANO_SHIELD | U4 | ENC28J60_NANO_SHIELD_ARDUINO | 1
2 | TG_WEMOS_D1_ESP32(CLONE) | U1 | WEMOS-D1 ESP32 | 1 | New SchematicLib |  |  | undefined
3 | USR-ES1 | U2 | USR-ES1 | 1 |  | USRIOT
4 | HDR-IDC-2.54-2X5P | P1 | IDC-TH_10P-P2.54_C5665 | 1 | IDC Box 2.54mm 2X5P | BOOMELE | LCSC | C5665 | Yes
5 | 1k | R1 | RES-TH_BD2.5-L6.2-P10.20-D0.6 | 1 | MF0207FTE52-1R5 | YAGEO | LCSC | C513633
6 | MP1584EN | U3 | MP1584EN | 1

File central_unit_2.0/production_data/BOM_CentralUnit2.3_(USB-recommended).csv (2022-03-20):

ID | Name (ext) | Designator | Footprint | Quantity | Manufacturer Part | Manufacturer | Supplier | Supplier Part | Price
1 | B5819W_C8598 (mod) | D25,D24,D22,D6,D9,D20,D3,D39,D4,D7,D8,D10,D11,D14,D15,D16,D17,D18,D19 | SOD-123_L2.8-W1.8-LS3.7-RD | 19 | B5819W SL | Changjiang Electronics Tech (CJ) | LCSC | C8598 | 0.044
2 | 1uF 50V (mod) | C8,C3,C54,C69,C70,C79,C80,C14,C36,C42 | C0603 | 10 | CL10A105KB8NNNC | Samsung Electro-Mechanics | LCSC | C15849 | 0.004
3 | 100nF 50V (mod) | C20,C55,C56,C78,C11,C5,C27,C1,C9,C33,C41,C24,C25 | C0603 | 13 | CC0603KRX7R9BB104 | YAGEO | LCSC | C14663 | 0.01
4 | 10K (mod) | R78,R79,R18,R53,R54,R61,R109,R113,R114,R10,R3,R63,R65,R74,R80,R96,R27,R30,R84,R8,R5,R13,R48,R44,R22,R35,R45,R47,R70 | R0603 | 29 | 0603WAF1002T5E | UNI-ROYAL(Uniroyal Elec) | LCSC | C25804 | 0.001
5 | 1K (mod) | R14,R211,R89,R106,R107,R108,R9,R59,R52,R31,R32,R34,R39,R49,R50,R64,R87,R88,R90,R91,R101,R103,R104,R105,R36,R23,R17,R15,R11,R12,R20,R21,R57,R58,R83,R69,R71 | R0603 | 37 | 0603WAF1001T5E | UNI-ROYAL(Uniroyal Elec) | LCSC | C21190 | 0.001
6 | CH340B (ext) | U22 | SOIC-16_L9.9-W3.9-P1.27-LS6.0-BL | 1 | CH340B | WCH | LCSC | C81010
8 | BC846AMTF (mod) | Q4,Q18,Q21,Q24 | SOT-23-3_L2.9-W1.3-P1.90-LS2.4-BR | 4 | MMBT2222A 1P | Changjiang Electronics Tech (CJ) | LCSC | C8512
9 | ZMM3V3 | D27 | LL-34_L3.5-W1.5-RD | 1 | ZMM3V3 | SEMTECH | LCSC | C8056 | 0.019
10 | 10 (mod) | R26,R98,C24,C25 | R0603 | 4 | 0603WAF100JT5E | UNI-ROYAL(Uniroyal Elec) | LCSC | C22859
12 | 1.8K (mod) | R60,R68,R24,R29,R258 | R0603 | 5 | 0603WAF1801T5E | UNI-ROYAL(Uniroyal Elec) | LCSC | C4177
13 | BZT52C18_C266571 (ext) | D21,D28 | SOD-123_L2.8-W1.8-LS3.7-RD | 2 | BZT52C18 | Bourne Semicon (Shenzhen) | LCSC | C266571
14 | 2N7002 (mod) | Q11,Q5,Q3,Q14,Q15 | SOT-23-3_L2.9-W1.3-P1.90-LS2.4-BR | 5 | 2N7002 | Changjiang Electronics Tech (CJ) | LCSC | C8545 | 0.023
20 | 22pF 50V (mod) | C81,C82 | C0603 | 2 | CL10C220JB8NNNC | Samsung Electro-Mechanics | LCSC | C1653
21 | AMS1117-3.3 | U4 | SOT-223-3_L6.5-W3.4-P2.30-LS7.0-BR | 1 | AMS1117-3.3 | AMS | LCSC | C6186
22 | white (mod) | 3V3,5V,12V | LED0603-R-RD | 3 | C2290 | Hubei KENTO Elec | LCSC | C2290
29 | SS34_C8678 | D2 | DO-214AC_L4.3-W2.7-LS5.3-RD | 1 | SS34 | MDD | LCSC | C8678 | 0.053
33 | 180uF (ext) | C15,C16,C12,C13,C6,C7 | CAP-SMD_BD8.0-L8.3-W8.3-RD | 6 | OVZ181M1DTR-0807 | Lelon | LCSC | C384618 | 0.389
35 | ZMM5V6 | D12,D13,D26 | LL-34_L3.5-W1.5-RD | 3 | ZMM5V6 | SEMTECH | LCSC | C8062 | 0.016
44 | green (mod) | RXD2,ACT,SCTRL,STEER,RXD1,RXD3 | LED0603-RD | 6 | 19-217/GHC-YR1S2/3T | Everlight Elec | LCSC | C72043 | 0.015
45 | blue (mod) | TXD2,GNSS,PORT,TXD1,TXD3 | LED0603-RD | 5 | 19-217/BHC-ZL1M2RY/3T | Everlight Elec | LCSC | C72041 | 0.015
50 | 5.1K (mod) | R6,R43,R46 | R0603 | 3 | 0603WAF5101T5E | UNI-ROYAL(Uniroyal Elec) | LCSC | C23186 | 0.001
51 | 2.2k (mod) | R25 | R0603 | 1 | 0603WAF2201T5E | UNI-ROYAL(Uniroyal Elec) | LCSC | C4190 | 0.001
53 | yellow (mod) | STEERINP,M1 | LED0603-RD | 2 | 19-213/Y2C-CQ2R2L/3T(CY) | Everlight Elec | LCSC | C72038 | 0.019
54 | orange (ext) | WORKINP,OUT1,M2,M3,WAS3 | LED0603-RD | 5 | FC-D1608HOK-600H | NATIONSTAR | LCSC | C84269 | 0.014
56 | 10uF 50V (mod) | C30 | C1206 | 1 | CL31A106KBHNNNE | Samsung Electro-Mechanics | LCSC | C13585 | 0.109
57 | 33pF 50V (mod) | C22,C23 | C0603 | 2 | CL10C330JB8NNNC | Samsung Electro-Mechanics | LCSC | C1663
58 | 10uF 25V (mod) | C28,C29,C31 | C0805 | 3 | CL21A106KAYNNNE | Samsung Electro-Mechanics | LCSC | C15850
59 | 10uF 25V (mod) | C65,C66,C67 | C0805 | 3 | CL21A106KAYNNNE | Samsung Electro-Mechanics | LCSC | C15850 | 0.011
60 | MMBT5401-C8326 | Q19,Q20,Q22,Q23,Q1,Q2,Q6 | SOT-23-3_L2.9-W1.3-P1.90-LS2.4-BR | 7 | MMBT5401 | CJ | LCSC | C8326 | 0.017
61 | 1K (mod) | R7,R16,R33 | R1206 | 3 | 1206W4F1001T5 | UNI-ROYAL(Uniroyal Elec) | LCSC | C4410
63 | 1K (mod) | R75,R76,R77,R37,R38,R56,R66,R67,R28 | R0603 | 9 | 0603WAF1001T5E | UNI-ROYAL(Uniroyal Elec) | LCSC | C21190 | 0.001
64 | 2.7k (mod) | R81 | R0603 | 1 | 0603WAF2701T5E | UNI-ROYAL(Uniroyal Elec) | LCSC | C13167
66 | FE1.1S (ext) | U18 | SSOP-28_L9.9-W3.9-P0.64-LS6.0-BL | 1 | FE1.1S | TERMINUS | LCSC | C9359
67 | ATMEGA328P-AU | U27 | TQFP-32_L7.0-W7.0-P0.80-LS9.0-BL | 1 | ATMEGA328P-AU | MICROCHIP | LCSC | C14877
68 | USB A/F 90° Outside the buckle straight foot (ext) | USB3,USB1,USB2 | USB-A-TH_USB-M-1_C2346 | 3 | USB A/F 90° Outside the buckle straight foot | ValuePro | LCSC | C2346 | 0.049
69 | TYPE-C-31-M-12 (ext) | USBC1 | USB-C_SMD-TYPE-C-31-M-12 | 1 | TYPE-C-31-M-12 | Rectangular Connectors - Contacts | LCSC | C165948 | 0.287
70 | 12MHz | X2 | OSC-SMD_4P-L3.2-W2.5-BL | 1 | X322512MSB4SI | YXC | LCSC | C9002
71 | 16MHz (ext) | X4 | OSC-SMD_4P-L2.0-W1.6-BL | 1 | X201616MPB4SC | Yangxing Tech | LCSC | C108156
72 | SMCJ33CA (ext) | D1 | SMC_L6.9-W5.9-LS7.9-BI | 1 | SMCJ33CA | Brightking Elec (TAIWAN) | LCSC | C310048 | 0.127
73 | red (mod) | F+5V,REV | LED0603-FD | 2 | KT-0603R | Hubei KENTO Elec | LCSC | C2286
74 | EL357N(B)(TA)-G | U1 | OPTO-SMD-4_L4.4-W4.1-P2.54-LS7.0-TL | 1 | EL357N(B)(TA)-G | EVERLIGHT | LCSC | C6649 | 0.056
75 | yellow (mod) | WAS2 | LED0603-RD | 1 | 19-213/Y2C-CQ2R2L/3T(CY) | Everlight Elec | LCSC | C72038 | 0.014
82 | 100pF 50V (mod) | C17,C18 | C0603 | 2 | CL10C101JB8NNNC | Samsung Electro-Mechanics | LCSC | C14858 | 0.005
83 | SED4060G (ext) | Q7,Q8 | POWERVDFN-8_L6.0-W5.0-P1.27-BL | 2 | SED4060G | SINO-IC | LCSC | C238671 | 0.402
84 | 750 (mod) | R19 | R1206 | 1 | 1206W4F7500T5E | UNI-ROYAL(Uniroyal Elec) | LCSC | C17985 | 0.004
85 | BTS50301EJAXUMA1 (ext) | U2,U14 | PG-DSO-8_L4.9-W3.9-P1.27-LS6.0-BL-EP | 2 | BTS50301EJAXUMA1 | Infineon Technologies | LCSC | C454924 | 1.885
86 | BTN8982TAA (ext) | U10 | TO-263-7_L10.2-W10.4-P1.27-LS14.4-B | 1 | BTN8982TAAUMA1 | Infineon | LCSC | C74175 | 4.91
88 | F0805 | F5 | F0805 | 1 | BSMD0805-050-24V | BHFUSE | LCSC | C910822
90 | 100uF | C2 | CAP-SMD_L3.5-W2.8 | 1 | TAJB107K006RNJ | AVX | LCSC | C16133 | 0.164
92 | 22 (mod) | R1 | R1206 | 1 | 1206W4F220JT5E | UNI-ROYAL(Uniroyal Elec) | LCSC | C17958 | 0.004
94 | BTN8982TAAUMA1 (ext) | U9 | TO-263-7_L10.2-W10.4-P1.27-LS14.4-B | 1 | BTN8982TAAUMA1 | Infineon | LCSC | C74175 | 4.91
95 | ADS1115IDGSR (ext) | U17 | MSOP-10_L3.0-W3.0-P0.50-LS5.0-BL | 1 | ADS1115IDGSR | TI | LCSC | C37593 | 5.305
102 | 47k (mod) | R51,R55,R72,R73,R62,R82,R92 | R0603 | 7 | 0603WAF4702T5E | UNI-ROYAL(Uniroyal Elec) | LCSC | C25819

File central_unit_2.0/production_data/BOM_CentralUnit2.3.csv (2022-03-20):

ID | Name (ext) | Designator | Footprint | Quantity | Manufacturer Part | Manufacturer | Supplier | Supplier Part | Price
1 | B5819W_C8598 (mod) | D25,D24,D22,D6,D9,D20,D3,D39,D4,D7,D8,D10,D11,D14,D15,D16,D17,D18,D19 | SOD-123_L2.8-W1.8-LS3.7-RD | 19 | B5819W SL | Changjiang Electronics Tech (CJ) | LCSC | C8598 | 0.044
2 | 1uF 50V (mod) | C10,C8,C3,C19,C21,C54,C57,C69,C70,C79,C80,C14,C36,C42 | C0603 | 14 | CL10A105KB8NNNC | Samsung Electro-Mechanics | LCSC | C15849 | 0.004
3 | 100nF 50V (mod) | C20,C304,C303,C302,C55,C56,C78,C11,C5,C27,C1,C9,C33,C41,C24,C25 | C0603 | 16 | CC0603KRX7R9BB104 | YAGEO | LCSC | C14663 | 0.01
4 | 10K (mod) | R78,R79,R2,R305,R304,R303,R302,R301,R300,R212,R208,R209,R18,R53,R54,R61,R109,R113,R114,R10,R3,R4,R40,R41,R63,R65,R74,R80,R96,R800,R27,R30,R84,R8,R5,R13,R48,R44,R22,R35,R261,R256,R45,R47,R70 | R0603 | 45 | 0603WAF1002T5E | UNI-ROYAL(Uniroyal Elec) | LCSC | C25804 | 0.001
5 | 1K (mod) | R260,R42,R259,R14,R200,R201,R203,R211,R89,R106,R107,R108,R9,R59,R52,R31,R32,R34,R39,R49,R50,R64,R87,R88,R90,R91,R101,R103,R104,R105,R36,R801,R23,R17,R15,R11,R12,R20,R21,R57,R58,R83 | R0603 | 42 | 0603WAF1001T5E | UNI-ROYAL(Uniroyal Elec) | LCSC | C21190 | 0.001
6 | CH340B (ext) | U5,U22,U23 | SOIC-16_L9.9-W3.9-P1.27-LS6.0-BL | 3 | CH340B | WCH | LCSC | C81010
7 | A2541WV-7P (ext) | PRGBOOT | HDR-TH_7P-P2.54-V-M | 1 | A2541WV-7P | Changjiang Connectors | LCSC | C225482
8 | BC846AMTF (mod) | Q4,Q10,Q13,Q18,Q21,Q24 | SOT-23-3_L2.9-W1.3-P1.90-LS2.4-BR | 6 | MMBT2222A 1P | Changjiang Electronics Tech (CJ) | LCSC | C8512
9 | ZMM3V3 | D27 | LL-34_L3.5-W1.5-RD | 1 | ZMM3V3 | SEMTECH | LCSC | C8056 | 0.019
10 | 10 (mod) | R26,R98,R203,C24,C25 | R0603 | 5 | 0603WAF100JT5E | UNI-ROYAL(Uniroyal Elec) | LCSC | C22859
11 | A2541WV-2P (ext) | NANO_OFF,ON1,CAN_PWR,CAN_PWR1,J3 | HDR-TH_P2.54-H-M_A2541WV-2P | 5 | A2541WV-2P | CJT(Changjiang Connectors) | LCSC | C225477
12 | 1.8K (mod) | R60,R68,R24,R29,R250,R257,R258 | R0603 | 7 | 0603WAF1801T5E | UNI-ROYAL(Uniroyal Elec) | LCSC | C4177
13 | BZT52C18_C266571 (ext) | D21,D250,D28 | SOD-123_L2.8-W1.8-LS3.7-RD | 3 | BZT52C18 | Bourne Semicon (Shenzhen) | LCSC | C266571
14 | 2N7002 (mod) | Q9,Q12,Q11,Q5,Q3,Q14,Q15 | SOT-23-3_L2.9-W1.3-P1.90-LS2.4-BR | 7 | 2N7002 | Changjiang Electronics Tech (CJ) | LCSC | C8545 | 0.023
15 | 100k (mod) | R253,R254,R255 | R0603 | 3 | 0603WAF1003T5E | UNI-ROYAL(Uniroyal Elec) | LCSC | C25803
17 | 1M (mod) | R252,R262,R210 | R0603 | 3 | 0603WAF1004T5E | UNI-ROYAL(Uniroyal Elec) | LCSC | C22935
18 | 32.768KHz (ext) | X300 | OSC-SMD_L3.2-W1.5 | 1 | DST310S 32.768KHz | KDS | LCSC | C93232
19 | BNO085 (ext) | U300 | BNO085 | 1
20 | 22pF 50V (mod) | C301,C300,C81,C82 | C0603 | 4 | CL10C220JB8NNNC | Samsung Electro-Mechanics | LCSC | C1653
21 | AMS1117-3.3 | U4 | SOT-223-3_L6.5-W3.4-P2.30-LS7.0-BR | 1 | AMS1117-3.3 | AMS | LCSC | C6186
22 | white (mod) | 3V3,5V,12V | LED0603-R-RD | 3 | C2290 | Hubei KENTO Elec | LCSC | C2290
23 | 51 (mod) | _R251,R202,R204,R205,R206 | R0603 | 4 | 0603WAF510JT5E | UNI-ROYAL(Uniroyal Elec) | LCSC | C23197
24 | 22uF 25V (mod) | C250 | C0805 | 1 | CL21A226MAQNNNE | Samsung Electro-Mechanics | LCSC | C45783 | 0.021
25 | 4.7nF 50V (mod) | C251,C252 | C0603 | 2 | 0603B472K500NT | FH(Guangdong Fenghua Advanced Tech) | LCSC | C53987
26 | 33pF 50V (mod) | C253 | C0603 | 1 | CL10C330JB8NNNC | Samsung Electro-Mechanics | LCSC | C1663
27 | 100nF 50V (mod) | C254 | C0603 | 1 | CC0603KRX7R9BB104 | YAGEO | LCSC | C14663
28 | 22uF 6.3V (mod) | C255,C256,C257 | C0603 | 3 | CL10A226MQ8NRNC | Samsung Electro-Mechanics | LCSC | C59461 | 0.008
29 | SS34_C8678 | D251,D2 | DO-214AC_L4.3-W2.7-LS5.3-RD | 2 | SS34 | MDD | LCSC | C8678 | 0.053
30 | 6.8uH (ext) | L250 | IND-SMD_L6.0-W6.0_SWPA6045S | 1 | SWPA6028S6R8MT | Sunlord | LCSC | C42261 | 0.067
31 | red (mod) | REV | LED0603-R-RD | 1 | KT-0603R | Hubei KENTO Elec | LCSC | C2286
32 | TPS54331DR | U250 | SOIC-8_L5.0-W4.0-P1.27-LS6.0-BL | 1 | TPS54331DR | TI | LCSC | C9865 | 0.382
33 | 180uF (ext) | C258,C15,C16,C12,C13,C6,C7 | CAP-SMD_BD8.0-L8.3-W8.3-RD | 7 | OVZ181M1DTR-0807 | Lelon | LCSC | C384618 | 0.389
34 | 2.2K (mod) | R207 | R0603 | 1 | 0603WAF2201T5E | UNI-ROYAL(Uniroyal Elec) | LCSC | C4190
35 | ZMM5V6 | D12,D13,D26 | LL-34_L3.5-W1.5-RD | 3 | ZMM5V6 | SEMTECH | LCSC | C8062 | 0.016
36 | 100nF 50V (mod) | C202 | C0603 | 1 | CC0603KRX7R9BB104 | YAGEO | LCSC | C14663
37 | 100nF 50V (mod) | C203,C210,C211,C212,C213,C206,C207,C208,C209 | C0603 | 9 | CC0603KRX7R9BB104 | YAGEO | LCSC | C14663 | 0.002
38 | 22nH (ext) | L200 | 402 | 1 | LQG15HS22NJ02D | MuRata | LCSC | C12670
39 | HR913550A (ext) | RJ200 | HR913550A | 1 | HR913550A | HANRUN | LCSC | C163507 | 1.061
40 | W5500 (ext) | U200 | QFP-48_LSA9.20-LSB9.20-PITCH0.50-TL | 1 | W5500 | WIZNET | LCSC | C32843
41 | 10nF 50V (mod) | C200,C201,C214,C215,C216,C217 | C0603 | 6 | 0603B103K500NT | FH(Guangdong Fenghua Advanced Tech) | LCSC | C57112
42 | 18pF 50V (mod) | C204,C205 | C0603 | 2 | CL10C180JB8NNNC | Samsung Electro-Mechanics | LCSC | C1647
43 | 25MHz | X1 | OSC-SMD_4P-L3.2-W2.5-BL | 1 | X322525MOB4SI | YXC | LCSC | C9006
44 | green (mod) | RXD2,ACT,SCTRL,STEER,RXD1,RXD3,RX485,RXCAN2 | LED0603-RD | 8 | 19-217/GHC-YR1S2/3T | Everlight Elec | LCSC | C72043 | 0.015
45 | blue (mod) | TXD2,GNSS,PORT,WIFI,TXD1,TXD3,TX485,TXCAN2 | LED0603-RD | 8 | 19-217/BHC-ZL1M2RY/3T | Everlight Elec | LCSC | C72041 | 0.015
46 | A2541WV-5P (ext) | USB-B | HDR-TH_5P-P2.54-V-M | 1 | A2541WV-5P | Changjiang Connectors | LCSC | C225480 | 0.081
47 | QWIIC SMD JST (ext) | QWIIC1 | QWIIC CONNECTOR | 1 | SM04B-SRSS-TB(LF)(SN) | JST Sales America | LCSC | C160404 | 0.157
48 | A2541WV-3P_C609572 (ext) | J1,J2 | HDR-TH_3P-P2.54-V-M | 2 | A2541WV-3P | CJT(Changjiang Connectors) | LCSC | C609572
49 | SMCJ5.0A (ext) | D5 | SMC_L6.9-W5.9-LS7.9-RD | 1 | SMCJ5.0A | Yenji | LCSC | C140785
50 | 5.1K (mod) | R6,R43,R46 | R0603 | 3 | 0603WAF5101T5E | UNI-ROYAL(Uniroyal Elec) | LCSC | C23186 | 0.001
51 | 2.2k (mod) | R25 | R0603 | 1 | 0603WAF2201T5E | UNI-ROYAL(Uniroyal Elec) | LCSC | C4190 | 0.001
52 | ESP32-WROOM-32U(16MB) (ext) | U6 | WIFIM-SMD_39P-L19.2-W18.0-P1.27 | 1 | ESP32-WROOM-32U(16MB) | Espressif Systems | LCSC | C529580
53 | yellow (mod) | STEERINP,M1 | LED0603-RD | 2 | 19-213/Y2C-CQ2R2L/3T(CY) | Everlight Elec | LCSC | C72038 | 0.019
54 | orange (ext) | WORKINP,OUT1,M2,M3,WAS3 | LED0603-RD | 5 | FC-D1608HOK-600H | NATIONSTAR | LCSC | C84269 | 0.014
55 | Testpoint (ext) | PT1 | TESTPOINT | 1
56 | 10uF 50V (mod) | C4,C30 | C1206 | 2 | CL31A106KBHNNNE | Samsung Electro-Mechanics | LCSC | C13585 | 0.109
57 | 33pF 50V (mod) | C22,C23 | C0603 | 2 | CL10C330JB8NNNC | Samsung Electro-Mechanics | LCSC | C1663
58 | 10uF 25V (mod) | C28,C29,C31 | C0805 | 3 | CL21A106KAYNNNE | Samsung Electro-Mechanics | LCSC | C15850
59 | 10uF 25V (mod) | C65,C66,C67 | C0805 | 3 | CL21A106KAYNNNE | Samsung Electro-Mechanics | LCSC | C15850 | 0.011
60 | MMBT5401-C8326 | Q19,Q20,Q22,Q23,Q1,Q2,Q6 | SOT-23-3_L2.9-W1.3-P1.90-LS2.4-BR | 7 | MMBT5401 | CJ | LCSC | C8326 | 0.017
61 | 1K (mod) | R7,R16,R33 | R1206 | 3 | 1206W4F1001T5 | UNI-ROYAL(Uniroyal Elec) | LCSC | C4410
63 | 1K (mod) | R69,R71,R75,R76,R77,R37,R38,R56,R66,R67,R28 | R0603 | 11 | 0603WAF1001T5E | UNI-ROYAL(Uniroyal Elec) | LCSC | C21190 | 0.001
64 | 2.7k (mod) | R81 | R0603 | 1 | 0603WAF2701T5E | UNI-ROYAL(Uniroyal Elec) | LCSC | C13167
65 | A2541WV-4P (ext) | SERIAL1 | HDR-TH_4P-P2.54-V | 1 | A2541WV-4P | Changjiang Connectors | LCSC | C225479 | 0.073
66 | FE1.1S (ext) | U18 | SSOP-28_L9.9-W3.9-P0.64-LS6.0-BL | 1 | FE1.1S | TERMINUS | LCSC | C9359
67 | ATMEGA328P-AU | U27 | TQFP-32_L7.0-W7.0-P0.80-LS9.0-BL | 1 | ATMEGA328P-AU | MICROCHIP | LCSC | C14877
68 | USB A/F 90° Outside the buckle straight foot (ext) | USB3,USB1,USB2 | USB-A-TH_USB-M-1_C2346 | 3 | USB A/F 90° Outside the buckle straight foot | ValuePro | LCSC | C2346 | 0.049
69 | TYPE-C-31-M-12 (ext) | USBC1 | USB-C_SMD-TYPE-C-31-M-12 | 1 | TYPE-C-31-M-12 | Rectangular Connectors - Contacts | LCSC | C165948 | 0.287
70 | 12MHz | X2 | OSC-SMD_4P-L3.2-W2.5-BL | 1 | X322512MSB4SI | YXC | LCSC | C9002
71 | 16MHz (ext) | X4 | OSC-SMD_4P-L2.0-W1.6-BL | 1 | X201616MPB4SC | Yangxing Tech | LCSC | C108156
72 | SMCJ33CA (ext) | D1 | SMC_L6.9-W5.9-LS7.9-BI | 1 | SMCJ33CA | Brightking Elec (TAIWAN) | LCSC | C310048 | 0.127
73 | red (mod) | F+5V | LED0603-FD | 1 | KT-0603R | Hubei KENTO Elec | LCSC | C2286
74 | EL357N(B)(TA)-G | U1 | OPTO-SMD-4_L4.4-W4.1-P2.54-LS7.0-TL | 1 | EL357N(B)(TA)-G | EVERLIGHT | LCSC | C6649 | 0.056
75 | yellow (mod) | WAS2 | LED0603-RD | 1 | 19-213/Y2C-CQ2R2L/3T(CY) | Everlight Elec | LCSC | C72038 | 0.014
76 | 47 (mod) | R802,R803 | R0603 | 2 | 0603WAF470JT5E | UNI-ROYAL(Uniroyal Elec) | LCSC | C23182 | 0.001
77 | TLC082ID | U800 | SOIC-8_L5.0-W4.0-P1.27-LS6.0-BL | 1 | TLC082ID | TI | LCSC | C1347544 | 0.162
78 | M12A 5pole female (ext) | INPUTS,STEERING | M12-A FEMALE 4-5POLE 90° | 2 |  | Binder, Escha | Digi-Key
79 | M8 4pole female (ext) | CAN,IMU,RS485,WAS | M8 FEMALE 4POLE 90° | 4 |  | Binder, Escha | Digi-Key
80 | M12A 5pole male (ext) | POWER | M12-A MALE 4-5POLE 90° | 1 |  | Binder, Escha | Digi-Key
81 | Ardfruit BNO085 (ext) | U3 | ADAFRUIT-BNO085 | 1 |  | Ardfruit
82 | 100pF 50V (mod) | C17,C18 | C0603 | 2 | CL10C101JB8NNNC | Samsung Electro-Mechanics | LCSC | C14858 | 0.005
83 | SED4060G (ext) | Q7,Q8 | POWERVDFN-8_L6.0-W5.0-P1.27-BL | 2 | SED4060G | SINO-IC | LCSC | C238671 | 0.402
84 | 750 (mod) | R19 | R1206 | 1 | 1206W4F7500T5E | UNI-ROYAL(Uniroyal Elec) | LCSC | C17985 | 0.004
85 | BTS50301EJAXUMA1 (ext) | U2,U14 | PG-DSO-8_L4.9-W3.9-P1.27-LS6.0-BL-EP | 2 | BTS50301EJAXUMA1 | Infineon Technologies | LCSC | C454924 | 1.885
86 | BTN8982TAA (ext) | U10 | TO-263-7_L10.2-W10.4-P1.27-LS14.4-B | 1 | BTN8982TAAUMA1 | Infineon | LCSC | C74175 | 4.91
87 | S2C-SMT 3.50/24/90LF 3.2SN BK BX (ext) | P1 | S2C-SMT 3.50/24/90LF 1.5SN BK BX | 1 | 1289960000 | WEIDMULLER | LCSC | C9137 | 0.12
88 | F0805 | F5,F2 | F0805 | 2 | BSMD0805-050-24V | BHFUSE | LCSC | C910822
89 | A2541WV-5P (ext) | H3,H2,H4,H5,H11,H12 | HDR-TH_5P-P2.54-V | 6 | A2541WV-5P | Changjiang Connectors | LCSC | C225480 | 0.081
90 | 100uF | C2 | CAP-SMD_L3.5-W2.8 | 1 | TAJB107K006RNJ | AVX | LCSC | C16133 | 0.164
91 | A2541WV-2X4P (ext) | H10 | HDR-TH_8P-P2.54-V-R2-C4-S2.54_A2541WV-2X4P | 1 | A2541WV-2x4P | Changjiang Connectors | LCSC | C225519 | 0.129
92 | 22 (mod) | R1 | R1206 | 1 | 1206W4F220JT5E | UNI-ROYAL(Uniroyal Elec) | LCSC | C17958 | 0.004
93 | KY3485LEEN (mod) | U8 | SO-8_L4.9-W3.9-P1.27-LS5.9-BL | 1 | SP3485EN-L/TR | MaxLinear | LCSC | C8963 | 0.679
94 | BTN8982TAAUMA1 (ext) | U9 | TO-263-7_L10.2-W10.4-P1.27-LS14.4-B | 1 | BTN8982TAAUMA1 | Infineon | LCSC | C74175 | 4.91
95 | ADS1115IDGSR (ext) | U17 | MSOP-10_L3.0-W3.0-P0.50-LS5.0-BL | 1 | ADS1115IDGSR | TI | LCSC | C37593 | 5.305
96 | TJA1051T/3/1J (ext) | U19 | SOIC-8_L4.9-W3.9-P1.27-LS6.0-BL | 1 | TJA1051T/3/1J | NXP | LCSC | C38695 | 3.726
97 | U10 (ext) | ARDUSIMPLE1 | ARDUSIMPLE_MECH_FLIPPED | 1 |  | Ardusimple
98 | U11 (ext) | ARDUSIMPLE2 | ARDUSIMPLE_MECH_FLIPPED | 1 |  | Ardusimple
99 | CMPS14 (ext) | U15 | CMPS14 | 1
100 | 1 | R263 | R1206 | 1 | 1206W4F100KT5E | UniOhm | LCSC | C17928 | 0.005
101 | AO3400A | Q250 | SOT-23-3_L2.9-W1.6-P1.90-LS2.8-BR | 1 | AO3400A | AOS | LCSC | C20917 | 0.132
102 | 47k (mod) | R51,R55,R72,R73,R62,R82,R92 | R0603 | 7 | 0603WAF4702T5E | UNI-ROYAL(Uniroyal Elec) | LCSC | C25819
103 | 4.7uF | C202 | C0603 | 1 | CL10A475KO8NNNC | Samsung Electro-Mechanics | LCSC | C19666
104 | THV8000DDFR | U8A | SOT65P280X110-8N | 1 | KY3485LEEN | Keysemi | LCSC | C428902 | 0.759
105 | 100uH | L1,L2 | IND-SMD_L4.5-W4.0_SM4532 | 2 | MSCD43-101KT | Meled(美莱) | LCSC | C915176 | 0.027

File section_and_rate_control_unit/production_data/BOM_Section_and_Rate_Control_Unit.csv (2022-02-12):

ID | Name (ext) | Designator | Footprint | Quantity | Manufacturer Part | Manufacturer | Supplier | Supplier Part | Price
1 | A2541WV-2P (ext) | REL,USBOFF,RS485,ON1,ON2 | HDR-TH_P2.54-H-M_A2541WV-2P | 5 | A2541WV-2P | CJT(Changjiang Connectors) | LCSC | C225477 | 0.032
2 | WJ250B-3.50-4P (ext) | SPEED,SENS1,SENS2,US1,US2,US3 | CONN-TH_4P-P3.50_WJ250B-3.50-4P | 6 | WJ250B-3.50-4P | ReliaPro | LCSC | C8455 | 0.145
3 | WJ142V-5.08-02P-14-00A (ext) | SECTION0.,SECTION1.,POWERIN,PRESSURE,SLOPE,SECTION2.,SECTION3.,SECTION4.,SECTION5.,SECTION6.,SECTION7.,VALVEMAIN | CONN-TH_2P-P5.08_WJ142V-5.08-2P | 12 | WJ142V-5.08-02P-14-00A | Ningbo Kangnex Elec | LCSC | C153288 | 0.145
4 | A2541WV-5P (ext) | CN3 | HDR-TH_5P-P2.54-V | 1 | A2541WV-5P | Changjiang Connectors | LCSC | C225480 | 0.081
5 | A2541WV-2X4P (ext) | H10 | HDR-TH_8P-P2.54-V-R2-C4-S2.54_A2541WV-2X4P | 1 | A2541WV-2x4P | Changjiang Connectors | LCSC | C225519 | 0.129
6 | JUMPER (ext) | JP7,JP8 | 1X03 | 2
7 | A2541WV-7P (ext) | PRGBOOT | HDR-TH_7P-P2.54-V-M | 1 | A2541WV-7P | Changjiang Connectors | LCSC | C225482 | 0.11
8 | HF115F/012-2ZS4AF (ext) | REL1,REL2,REL3,REL4,REL5,REL6,REL7,REL8,REL9,REL10,REL11,REL12,REL13 | RELAY-TH_HF115F-XXX-2XX4XX | 13 | HF115F/012-2ZS4AF | HF(Xiamen Hongfa Electroacoustic) | LCSC | C882372 | 1.579
9 | SMCJ33CA (ext) | D16 | SMC_L6.9-W5.9-LS7.9-BI | 1 | SMCJ33CA | Brightking Elec (TAIWAN) | LCSC | C310048 | 0.129
10 | 22uF 25V (mod) | C250,C14,C15,C17 | C0805 | 4 | CL21A226MAQNNNE | Samsung Electro-Mechanics | LCSC | C45783
11 | 4.7nF 50V (mod) | C251,C252 | C0603 | 2 | 0603B472K500NT | FH(Guangdong Fenghua Advanced Tech) | LCSC | C53987
12 | 33pF 50V (mod) | C253 | C0603 | 1 | CL10C330JB8NNNC | Samsung Electro-Mechanics | LCSC | C1663
13 | 100nF 50V (mod) | C254,C26,C27 | C0603 | 3 | CC0603KRX7R9BB104 | YAGEO | LCSC | C14663
14 | 22uF 6.3V (mod) | C255,C256,C257 | C0603 | 3 | CL10A226MQ8NRNC | Samsung Electro-Mechanics | LCSC | C59461 | 0.009
15 | 1uF 50V (mod) | C258,C12,C57,C74,C75 | C0603 | 5 | CL10A105KB8NNNC | Samsung Electro-Mechanics | LCSC | C15849 | 0.004
16 | SS34_C8678 | D251 | DO-214AC_L4.3-W2.7-LS5.3-RD | 1 | SS34 | MDD | LCSC | C8678 | 0.053
17 | 6.8uH (ext) | L250 | IND-SMD_L6.0-W6.0_SWPA6045S | 1 | SWPA6028S6R8MT | Sunlord | LCSC | C42261 | 0.066
18 | 1.3 (ext) | R64,R251 | R1206 | 2 | AECR1206F1R30T9 | ResistorToday | LCSC | C352126 | 0.011
19 | 1.8K (mod) | R65,R257 | R0603 | 2 | 0603WAF1801T5E | UNI-ROYAL(Uniroyal Elec) | LCSC | C4177
20 | 1M (mod) | R252 | R0603 | 1 | 0603WAF1004T5E | UNI-ROYAL(Uniroyal Elec) | LCSC | C22935 | 0.001
21 | 150K (mod) | R253,R4,R7,R8,R11,R14,R17,R23,R63,R70,R71,R73,R74,R75,R76,R80,R81,R82,R84 | R0603 | 19 | 0603WAF1503T5E | UNI-ROYAL(Uniroyal Elec) | LCSC | C22807 | 0.001
22 | 100k (mod) | R254,R255 | R0603 | 2 | 0603WAF1003T5E | UNI-ROYAL(Uniroyal Elec) | LCSC | C25803
23 | 10K (mod) | R256,R90,R91,R92,R93 | R0603 | 5 | 0603WAF1002T5E | UNI-ROYAL(Uniroyal Elec) | LCSC | C25804
24 | red (mod) | REV | LED0603-R-RD | 1 | KT-0603R | Hubei KENTO Elec | LCSC | C2286 | 0.005
25 | TPS54331DR | U250 | SOIC-8_L5.0-W4.0-P1.27-LS6.0-BL | 1 | TPS54331DR | TI | LCSC | C9865 | 0.326
26 | 600Ω | L1 | L0805 | 1 | GZ2012D601TF | Sunlord | LCSC | C1017 | 0.008
27 | white (mod) | 5V,12V,3V3 | LED0603-R-RD | 3 | C2290 | Hubei KENTO Elec | LCSC | C2290 | 0.011
28 | BC856 (mod) | Q32,Q8,Q10,Q21,Q22,Q23,Q24,Q25,Q26,Q27,Q28,Q29,Q30,Q31 | SOT-23-3_L2.9-W1.3-P1.90-LS2.4-BR | 14 | S9015 | Changjiang Electronics Tech (CJ) | LCSC | C2149 | 0.029
29 | BC846 (mod) | Q33,Q1,Q2,Q3,Q4,Q5,Q6,Q7,Q9,Q11,Q12,Q13,Q14,Q15,Q16 | SOT-23-3_L2.9-W1.3-P1.90-LS2.4-BR | 15 | MMBT2222A 1P | Changjiang Electronics Tech (CJ) | LCSC | C8512 | 0.019
30 | 10K (mod) | R47,R48,R49,R33,R50,R51,R52,R54,R55,R56,R58,R59,R61 | R0603 | 13 | 0603WAF1002T5E | UNI-ROYAL(Uniroyal Elec) | LCSC | C25804 | 0.001
31 | 100nF 50V (mod) | C25,C20,C21,C22,C23,C24,C13,C58,C59,C73 | C0603 | 10 | CC0603KRX7R9BB104 | YAGEO | LCSC | C14663 | 0.008
32 | B5819W_C8598 (mod) | D17,D18,D19,D20,D15,D24,D25 | SOD-123_L2.8-W1.8-LS3.7-RD | 7 | B5819W SL | Changjiang Electronics Tech (CJ) | LCSC | C8598 | 0.044
33 | 5.1K (mod) | R44,R45,R46,R53 | R0603 | 4 | 0603WAF5101T5E | UNI-ROYAL(Uniroyal Elec) | LCSC | C23186 | 0.001
34 | KY3485LEEN (mod) | U5,U10,U11,U12,U14 | SO-8_L4.9-W3.9-P1.27-LS5.9-BL | 5 | SP3485EN-L/TR | MaxLinear | LCSC | C8963 | 0.679
35 | 10nF 50V (mod) | C7,C9,C18,C19,C1,C2,C3,C4,C5,C6,C8,C10,C11,C16,C35 | C0603 | 15 | 0603B103K500NT | FH(Guangdong Fenghua Advanced Tech) | LCSC | C57112 | 0.002
36 | green (mod) | SECTION7,RXD1,SECT0/SPEED,SECTION1,SECTION2,SECTION3,SECTION4,SECTION5,SECTION6,SENSOR1,SENSOR2,MAINLED | LED0603-RD | 12 | 19-217/GHC-YR1S2/3T | Everlight Elec | LCSC | C72043 | 0.015
37 | 1N4148WS T4 (ext) | D2,D3,D4,D5,D6,D7,D8,D9,D10,D11,D12,D13,D14 | SOD-323_L1.8-W1.3-LS2.5-RD | 13 | 1N4148WS T4 | CJ | LCSC | C2128 | 0.014
38 | 1K (mod) | R20,R26,R36,R37,R38,R39,R40,R41,R42,R43,R1,R2,R3,R5,R6,R9,R10,R12,R13,R15,R16,R18,R19,R21,R22,R24,R25,R27,R28,R29,R30,R31,R32,R34,R35,R57,R60,R62,R72,R83,R89,R106,R107,R108 | R0603 | 44 | 0603WAF1001T5E | UNI-ROYAL(Uniroyal Elec) | LCSC | C21190 | 0.001
39 | LM393DR2G | U1,U2 | SOIC-8_L5.0-W4.0-P1.27-LS6.0-BL | 2 | LM393DR2G | ON | LCSC | C7955 | 0.162
40 | TYPE-C-31-M-12 (ext) | USBC | USB-C_SMD-TYPE-C-31-M-12 | 1 | TYPE-C-31-M-12 | Rectangular Connectors - Contacts | LCSC | C165948 | 0.287
41 | SPDT SWITCH (ext) | ALL_ON,SW1,SW2,SW3,SW4,SW5,SW6,SW7,SW8,PRESS,WORK,STEER,SLOPE_ | SPDT SWITCH ON ON | 13 | Switch SPDT
42 | 10uF 25V (mod) | C65,C66,C67 | C0805 | 3 | CL21A106KAYNNNE | Samsung Electro-Mechanics | LCSC | C15850
43 | 22pF 50V (mod) | C76,C77 | C0603 | 2 | CL10C220JB8NNNC | Samsung Electro-Mechanics | LCSC | C1653 | 0.004
44 | SS14FL_C118876 (ext) | D1 | SOD-123F_L2.8-W1.8-LS3.7-RD | 1 | SS14FL | ON Semicon | LCSC | C118876
45 | TM1637 7-SEGMET 4-DIGIT 0.56" (ext) | DP1 | TM1637 4-DIGITS* | 1
46 | HDMI-019S (ext) | HDMI | HDMI-SMD_HDMI-019S | 1 | HDMI-019S | SOFNG | LCSC | C111617 | 0.302
47 | 2N7002 (mod) | Q17,Q20 | SOT-23-3_L2.9-W1.3-P1.90-LS2.4-BR | 2 | 2N7002 | Changjiang Electronics Tech (CJ) | LCSC | C8545 | 0.023
48 | BC846AMTF (mod) | Q18,Q19 | SOT-23-3_L2.9-W1.3-P1.90-LS2.4-BR | 2 | MMBT2222A 1P | Changjiang Electronics Tech (CJ) | LCSC | C8512 | 0.08
49 | 100K (mod) | R77,R78,R79 | R0603 | 3 | 0603WAF1003T5E | UNI-ROYAL(Uniroyal Elec) | LCSC | C25803 | 0.007
50 | blue (mod) | TXD1,WIFI | LED0603-RD | 2 | 19-217/BHC-ZL1M2RY/3T | Everlight Elec | LCSC | C72041 | 0.015
51 | 78L12G-AB3-R | U3 | SOT-89-3_L4.5-W2.5-P1.50-LS4.2-BR | 1 | 78L12G-AB3-R | UTC | LCSC | C75501 | 0.122
52 | AMS1117-3.3 | U4 | SOT-223-3_L6.5-W3.4-P2.30-LS7.0-BR | 1 | AMS1117-3.3 | AMS | LCSC | C6186 | 0.159
53 | ESP32-WROOM-32U(16MB) (ext) | U6 | WIFIM-SMD_39P-L19.2-W18.0-P1.27 | 1 | ESP32-WROOM-32U(16MB) | Espressif Systems | LCSC | C529580 | 6.859
54 | CH340B (ext) | U23 | SOIC-16_L9.9-W3.9-P1.27-LS6.0-BL | 1 | CH340B | WCH | LCSC | C81010 | 1.19
55 | ATMEGA328P-AU | U26 | TQFP-32_L7.0-W7.0-P0.80-LS9.0-BL | 1 | ATMEGA328P-AU | MICROCHIP | LCSC | C14877 | 9.961
56 | 16MHz (ext) | X3 | OSC-SMD_4P-L2.0-W1.6-BL | 1 | X201616MPB4SC | Yangxing Tech | LCSC | C108156 | 0.138
57 | 15K (mod) | R66,R67,R68,R69,R85,R86,R87,R88 | R0603 | 8 | 0603WAF1502T5E | UNI-ROYAL(Uniroyal Elec) | LCSC | C22809 | 0.001
58 | THV8000DDFR | U7 | SOT65P280X110-8N | 1 | KY3485LEEN | Keysemi | LCSC | C428902 | 0.693
59 | 100uH | L2,L3 | IND-SMD_L4.5-W4.0_SM4532 | 2 | MSCD43-101KT | Meled(美莱) | LCSC | C915176 | 0.027

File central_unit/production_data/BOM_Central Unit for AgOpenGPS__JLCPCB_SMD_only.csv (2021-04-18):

ID | Name | Designator | Footprint | Quantity | Manufacturer Part | Manufacturer | Supplier | Supplier Part | LCSC Assembly | JLCPCB SMD
 | 0 | L8,L2 | R0603 | 2 | 0603WAF0000T5E | UniOhm | LCSC | C21189 | Yes | Yes | for EMC: | 1500Ω | L8 | L0603 | 1 | GZ1608D152CTF | Sunlord | LCSC | C96693
 | 10 | R83 | R0603 | 1 | RTT03100JTP | RALEC | LCSC | C103203
 | 120 | R60,R65,R92 | R1206 | 3 | RTT06121JTP | RALEC | LCSC | C104621 |  |  | for EMC: | 120 | R92,R65,R60 | R1206 | 3 | RTT06121JTP | RALEC | LCSC | C104621
 | 560 | R36,R44,R47 | R0603 | 3 | RTT03561JTP | RALEC | LCSC | C103717
 | 100nF | C3,C4,C7,C8,C9,C11,C16,C19,C27,C28,C29,C33,C38,C45,C48,C55,C58,C59 | C0603 | 18 | CC0603JRX7R8BB104 | YAGEO | LCSC | C327087
 | 100pF | C61 | C0603 | 1 | CL10C101JB8NNNC | SAMSUNG | LCSC | C14858 | Yes | Yes | option: | SMCJ33CA | D1 | SMC_L6.9-W5.9-LS7.9-BI | 1 | SMCJ33CA | Brightking Elec (TAIWAN) | LCSC | C310048
 | 10K | R2,R8,R15,R16,R18,R19,R33,R34,R35,R39,R48,R49,R50,R51,R70,R73,R74,R77,R78,R79,R80,R82,R93,R94,R5,R13 | R0603 | 26 | RTT03103JTP | RALEC | LCSC | C103210
 | 10uF | C12,C10,C26 | C0805 | 3 | 0805X106K100 | WTC | LCSC | C105505
 | 10uF | C17,C18,C30 | C1206 | 3 | TCC1206X7R106K250HT | CCTC | LCSC | C380364
 | 10uH | L7,L1 | IND-SMD_L5.4-W5.2 | 2 | MWSA0503-100MT | Sunlord | LCSC | C139506 | Yes | Yes
 | 12MHz | X2,X3 | OSC-SMD_4P-L3.2-W2.5-BL | 2 | X322512MSB4SI | YXC | LCSC | C9002 |  | Yes
 | 16MHz | X1 | OSC-SMD_4P-L2.0-W1.6-BL | 1 | X201616MPB4SC | Yangxing Tech | LCSC | C108156
 | 1K | R3,R4,R14,R29,R30,R37,R38,R64,R66,R67,R68,R69,R84,R85,R86,R87,R88,R89,R102,R6,R7,R9,R10,R11,R12,R20,R21,R22,R23,R31,R32,R52,R56,R57,R58,R59,R75,R76,R90,R91,R98,R104,R95,R96 | R0603 | 44 | RTT03102JTP | RALEC | LCSC | C103209
 | 1nF | C62,C24,C25,C57 | C0603 | 4 | 0603CG102F500NT | FH(Guangdong Fenghua Advanced Tech) | LCSC | C507408
 | 1uF | C15,C54,C51,C50,C49,C40,C46,C43,C42,C41,C35,C47,C14,C2,C36,C22,C34,C56 | C0603 | 18 | CL10A105KP8NNNC | SAMSUNG | LCSC | C26413
 | 2.7k | R81,R71,R72,R1,R24 | R0603 | 5 | RTT03272JTP | RALEC | LCSC
 | 22pF | C6,C5 | C0603 | 2 | TCC0603COG220J500CT | CCTC | LCSC | C376775
 | 22uF | C60,C53,C21,C52,C20 | C0805 | 5 | CL21A226MAQNNNE | SAMSUNG | LCSC | C45783
 | 2k2 | R27,R42,R41,R45,R40,R99,R26,R25 | R0603 | 8 | RTT03222JTP | RALEC | LCSC | C103203
 | 2N7002WT1G | Q5,Q4,Q3,Q1 | SOT-323-3_L2.0-W1.3-P1.30-LS2.1-BR | 4 | 2N7002WT1G | ON Semicon | LCSC | C12778 |  | Yes
 | 33pF | C13,C23,C39,C37 | C0603 | 4 | CL10C330JB8NNNC | SAMSUNG | LCSC | C1663
 | 470uF | C32,C31 | CAP-SMD_BD10.0-L10.3-W10.3-FD | 2 | HV471M016F105R | CapXon | LCSC | C59924
 | 5.1K | R46,R43 | R0603 | 2 | 0603WAF5101T5E | UniOhm | LCSC | C23186 | Yes | Yes
 | 75K | R17,R100 | R0603 | 2 | 0603WAF7502T5E | UniOhm | LCSC | C23242 | Yes | Yes
 | ADS1115IDGSR | U17 | MSOP-10_L3.0-W3.0-P0.50-LS5.0-BL | 1 | ADS1115IDGSR | TI | LCSC | C37593 | Yes
 | ATMEGA328P-AU | U5 | TQFP-32_L7.0-W7.0-P0.80-LS9.0-BL | 1 | ATMEGA328P-AU | MICROCHIP | LCSC | C14877 |  | Yes
 | BC856BW,115 | Q7,Q2,Q9,Q10,Q11,Q12 | SOT-323-3_L2.2-W1.3-P1.30-LS2.2-BR | 6 | BC856BW,115 | Nexperia | LCSC | C28063 | Yes
 | BM06B-GHS-TBT | ARDU1 | CONN-TH_SM06B-GHS-TB | 1 | BM06B-GHS-TBT LF SN | JST Sales America | LCSC
 | BSMD0603-050-6V | F7,F5,F1,F6,F4,F2,F3 | F0603 | 7 | BSMD0603-050-6V | BHFUSE | LCSC | C883095
 | BTN8982TAAUMA1 | U9,U10 | TO-263-7_L10.2-W10.4-P1.27-LS14.4-B | 2 | BTN8982TAAUMA1 | Infineon | LCSC | C74175
 | BTS50301EJAXUMA1 | xU14 | PG-DSO-8_L4.9-W3.9-P1.27-LS6.0-BL-EP | 1 | BTS50301EJAXUMA1 | Infineon Technologies | LCSC | C454924 |  |  | remove ‘x‘ in front of ‘U14‘ in column C and delete R59 if 6/2 valve should be controlled
 | CDSOT23-T24CAN | D5,D6,D7 | SOT-23_L2.9-W1.3-P0.95-LS2.4-BR | 3 | CDSOT23-T24CAN | Yenji Elec | LCSC | C252430 | Yes
 | CH340B | U3,U6,U19 | SOIC-16_L9.9-W3.9-P1.27-LS6.0-BL | 3 | CH340B | WCH | LCSC | C81010
 | FE1.1S | U2 | SSOP-28_L9.9-W3.9-P0.64-LS6.0-BL | 1 | FE1.1S | TERMINUS | LCSC | C9359 |  | Yes
 | HSBA4048 | Q8 | POWERPAK-SO-8_L6.2-W5.2-P1.27-BR-EP | 1 | HSBA4048 | HUASHUO | LCSC | C508827 |  |  | 2nd source e. g.: SINO-IC SED4060G, part C238671
 | KH-TYPE-C-16P | DC/AUX,TO_PC | USB-C-SMD_KH-TYPE-C-16P | 2 | KH-TYPE-C-16P | Shenzhen Kinghelm Elec | LCSC | C709357
 | KY3485LEEN | U8 | SO-8_L4.9-W3.9-P1.27-LS5.9-BL | 1 | KY3485LEEN | Keysemi | LCSC | C428902
 | LED blue | TX485,TXD,GNSS_,AUX1,LED4,TXCAN1,LED2,TXCAN,WIFI | LED0603-RD | 9 | 19-217/BHC-ZL1M2RY/3T | Everlight Elec | LCSC | C72041 |  | Yes
 | LED green | RXD,RX485,USB:,LED3,ANT1,ANT2,LED1,RXCAN1,DIFF,AUX0,ARDU,RXCAN | LED0603-RD | 12 | 19-217/GHC-YR1S2/3T | Everlight Elec | LCSC | C72043 |  | Yes
 | LED orange | CHB,WAS3,M2 | LED0603-RD | 3 | FC-D1608HOK-600H | NATIONSTAR | LCSC | C84269 |  | Yes
 | LED red | LED,FSER,FGNSS,FROT,FWAS,FINP,FCAN,FCAN1 | LED0603-FD | 8 | KT-0603R | Hubei KENTO Elec | LCSC | C2286
 | LED white | MOT,5V,12V,3V3 | LED0603-RD | 4 |  | Hubei KENTO Elec | LCSC | C2290 |  | Yes
 | LED yellow | REMOTE,M1,CHA,WAS2,STEER,WORK | LED0603-RD | 6 | 19-213/Y2C-CQ2R2L/3T(CY) | Everlight Elec | LCSC | C72038 |  | Yes
 | LPC54616J512BD100 | U11 | TQFP-100_14X14X05P | 1 | LPC54616J512BD100 |  | Digi-Key | 568-13457-ND
 | MMA8452QR1_C11360 | U18 | QFN-16_L3.0-W3.0-P0.50-TL_MMA8452QR1 | 1 | MMA8452QR1 | FREESCALE | LCSC | C11360 | Yes
 | QWIIC SMD JST | QWIIC | QWIIC CONNECTOR | 1 | SM04B-SRSS-TB(LF)(SN) | JST Sales America | LCSC | C160404
 | SS54 | D3 | SMA_L4.4-W2.8-LS5.4-RD | 1 | SS54 | Diodes | LCSC | C22452 |  | Yes
 | TJA1051T/3/1J | U12,U7 | SO-8_L4.9-W3.9-P1.27-LS5.9-BL | 2 | TJA1051T/3/1J | NXP | LCSC | C38695
 | TPS54302DDCR_C311983 | U13,U4 | SOT-23-6_L2.9-W1.6-P0.95-LS2.8-BL | 2 | TPS54302DDCR | Texas Instruments | Texas Instruments | C311983
 | ZXMS6004FFTA | Q6 | SOT-23-3_L2.9-W1.6-P1.90-LS2.8-BR | 1 | ZXMS6004FFTA | Diodes Incorporated | LCSC | C95063
 | HDR-IDC-2.54-2X5P | P1 | IDC-TH_10P-P2.54_C5665 | 1 | IDC Box 2.54mm 2X5P | BOOMELE | LCSC | C5665 |  | Yes
 | A2541WV-3P_C609572 | H1 | HDR-TH_3P-P2.54-V-M | 1 | A2541WV-3P | CJT(Changjiang Connectors) | LCSC | C609572 |  | Yes | expand
 | A2541WV-4P | J8 | HDR-TH_4P-P2.54-V | 1 | A2541WV-4P | Changjiang Connectors | LCSC | C225479
 | A2541WV-5P | CN3 | HDR-TH_5P-P2.54-V | 1 | A2541WV-5P | Changjiang Connectors | LCSC | C225480 |  | Yes | expand |  | manualWeld
 | A2541WV-2P | J7 | HDR-TH_P2.54-H-M_A2541WV-2P | 1 | A2541WV-2P | CJT(Changjiang Connectors) | LCSC | C225477
 | 10K | R28,R55,R54,R53,R63,R62,R61 R1206 | R1206 | 7 | 1206W4F1002T5E | Uniroyal Elec | LCSC | C17902 |  |  | for FS: 8.2K R28,R55,R54,R53,R63,R62,R61 RES-SMD_L3.5-W1.5 7 MElF-MFR02041/4WS130ΩFT50 Thunder Component

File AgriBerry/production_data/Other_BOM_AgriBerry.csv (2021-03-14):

ID | Name | Designator | Footprint | Quantity | Manufacturer Part | Manufacturer | Supplier | Supplier Part | _Price | JLCPCB SMD | LCSC Assembly | Assembly Type | Paste Type | Annotation
2 | SM06B-GHS-TB(LF)(SN) | ARDU1 | CONN-TH_SM06B-GHS-TB-LF-SN | 1 | SM06B-GHS-TB(LF)(SN) | JST Sales America | LCSC | C133065 |  |  |  |  |  | for Ardusimple via Pixhawk connectors
3 | SM06B-GHS-TB(LF)(SN) | ARDU2 | CONN-TH_SM06B-GHS-TB-LF-SN | 1 | SM06B-GHS-TB(LF)(SN) | JST Sales America | LCSC | C133065 |  |  |  |  |  | for 2nd Ardusimple via Pixhawk connectors
11 | 470uF | C22 | CAP-TH_BD6.3-P2.50-D1.0-FD | 1 | 470uF 6.3VGreen high frequency 6.3*7 | ValuePro | LCSC | C43328 |  |  | Yes | manualWeld | expand | electrolytic cap (optional)
14 | 100uF | C31,C32 | CAP-TH_BD8.0-P3.50-D1.0-FD | 2 | 100uF 35V 8*12 | ValuePro | LCSC | C45077 |  |  |  |  |  | electrolytic cap (optional)
17 | RASPBERRYPI-B+-GPIO | CN1 | HDR-F-2.54_2X20 | 1 |  |  |  |  |  |  |  |  |  | either female on bottom or male top (needs 40pol ribbon cable in that case, too)
24 | A2541WV-8P | H1 | HDR-TH_8P-P2.54-V-M | 1 | A2541WV-8P | Changjiang Connectors | LCSC | C225483 |  |  |  | manualWeld | expand | for Ardusimple piggyback
25 | A2541WV-10P | H2 | HDR-TH_10P-P2.54-V | 1 | A2541WV-10P | Changjiang Connectors | LCSC | C225485 |  |  | Yes | manualWeld | expand | for Ardusimple piggyback
26 | A2541WV-2X2P | H3 | HDR-TH_4P-P2.54-V-R2-C2-S2.54_A2541WV-2X2P | 1 | A2541WV-2x2P | Changjiang Connectors | LCSC | C225517 |  |  | Yes | manualWeld | expand | for Ardusimple piggyback
27 | A2541WV-2P | H4,J1 | HDR-TH_P2.54-H-M_A2541WV-2P | 2 | A2541WV-2P | CJT(Changjiang Connectors) | LCSC | C225477 |  |  |  |  |  | for Ardusimple piggyback
30 | A2541WV-4P | J8 | HDR-TH_4P-P2.54-V | 1 | A2541WV-4P | Changjiang Connectors | LCSC | C225479 |  |  |  |  |  | for power switch
36 | S2C-SMT 3.50/24/90LF 1.5SN BK BX | P1 | S2C-SMT 3.50/24/90LF 1.5SN BK BX | 1 | 1289960000 | WEIDMULLER | LCSC | C9137 |  |  | Yes | manualWeld | expand | + B2CF 3.50/24/180LH SN BK BX (1372870000)
41 | QWIIC SMD JST | QWIIC2 | QWIIC CONNECTOR | 1 | SM04B-SRSS-TB(LF)(SN) | JST Sales America | LCSC | C160404 |  |  |  |  |  | if QWIIC is needed
62 | A2541WV-4P | SERIAL1 | HDR-TH_4P-P2.54-V | 1 | A2541WV-4P | Changjiang Connectors | LCSC | C225479 |  |  |  |  |  | option for RS232, etc
72 | CMPS14 | U24 | CMPS14 | 1 |  |  |  |  |  |  |  |  |  | IMU module (alternative to U25)
 | RASPBERRY PI 4B |  |  | 1 |  | Raspberry foundation |  |  |  |  |  |  |  | Raspberry

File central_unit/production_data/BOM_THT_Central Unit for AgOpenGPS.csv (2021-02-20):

ID | Name | Designator | Footprint | Quantity | Manufacturer | Manufacturer Part # | Distributors e. g. | Example link Europe | Example link US/worldwide
7 | M12 4pole female | GNSS | M12-D FEMALE 4POLE 90° | 1 | Binder, Escha, Conec, etc. | Conec: 43-01229 | Mouser, Reichelt | https://www.reichelt.de/sal-m-12-4-pol-buchse-gewinkelt-conec-43-01229-p249156.html?CCOUNTRY=445&LANGUAGE=en | https://www.mouser.com/_/?Keyword=43-01229
8 | 1315-1206G0M075CP01 | CN6 | HDR-SMD_12P-P1.27-V-M-R2-C6-S7.50 | 1 | many
10 | A2541WV-2X3P | CN9,CN8,CN10 | HDR-TH_6P-P2.54-V-R2-C3-S2.54_A2541WV-2X3P |  | many |  |  | https://www.reichelt.de/de/en/pin-headers-2-54-mm-1x50-straight-mpe-087-1-050-p119891.html?&nbc=1
13 | TG_WEMOS_D1_ESP32(CLONE) | U1 | WEMOS-D1 ESP32 | 1 | many |  | Aliexpress, Digi-Key, AZ-delivery | https://de.aliexpress.com/item/32834982479.html | https://www.az-delivery.de/en/products/esp32-d1-mini
13 | socket for WEMOS | U1 | Female 2.54mm dual row |  | many |  |  | https://www.reichelt.de/de/en/female-connector-2-54mm-2x36-separable-tinned-fis-bl2-72z-p292529.html?nbc=1
18 | M12A 5pole female | INPUTS,STEERING | M12-A FEMALE 4-5POLE 90° | 2 | Binder, Escha, Conec, etc. | Conec: 43-01198 | Mouser, Reichelt | https://www.reichelt.de/de/en/sal-m-12-5-pin-socket-angled-conec-43-01198-p249151.html?trstct=pol_8&nbc=1 | https://www.mouser.com/_/?Keyword=43-01198
22 | M8 4pole female | CANB,CAN,ROTARY/485 | M8 FEMALE 4POLE 90° | 3 | Binder, Escha, Conec, etc. | Conec: 42-01427 | Mouser, Reichelt | https://www.reichelt.de/de/en/sal-m-8-4-pin-socket-angled-conec-42-01427-p249166.html?trstct=pol_3&nbc=1 | https://www.mouser.com/_/?Keyword=42-01427
29 | A2541WV-4P | J8,J6 | HDR-TH_4P-P2.54-V |  | many |  |  | https://www.reichelt.de/de/en/pin-headers-2-54-mm-1x50-straight-mpe-087-1-050-p119891.html?&nbc=1
32 | CMPS14 | U15 | CMPS14 | 1 |  |  |  | https://www.robotshop.com/en/tilt-compensated-magnetic-compass-cmps14.html
33 | A/F90_C109354 | USB1 | USB-A-TH_USB-A-F-2 | 1 | many
37 | A2541WV-2X2P | J2,CN16,J3 | HDR-TH_4P-P2.54-V-R2-C2-S2.54_A2541WV-2X2P |  | many |  |  | https://www.reichelt.de/de/en/pin-headers-2-54-mm-1x50-straight-mpe-087-1-050-p119891.html?&nbc=1
41 | HDR-IDC-2.54-2X3P | P1 | IDC-TH_6P-P2.54_C11214 |  | many |  |  | https://www.reichelt.de/de/en/pin-headers-2-54-mm-1x50-straight-mpe-087-1-050-p119891.html?&nbc=1
42 | M12A 5pole male | POWER | M12-A MALE 4-5POLE 90° | 1 | Binder, Escha, Conec, etc. | Conec: 43-01206 | Mouser, Reichelt | https://www.reichelt.de/de/en/sal-m-12-5-pin-built-in-plug-angled-conec-43-01206-p249155.html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 | https://www.mouser.com/_/?Keyword=43-01206
45 | 4x1 push_in connector | CN17,CN5,CN4,CN18,CN1,CN2,CN11,CN12 | S2C-SMT 3.50/04/180G 3.5SN BK RL | 8 | Weidmuller | 1290030000 | Weidmüller via Digi-Key, Conrad | https://www.conrad.de/de/p/weidmueller-stiftgehaeuse-platine-1290030000-222-st-1949974.html | https://www.digikey.com/en/products/detail/weidmüller/1290030000/4015271
45 | 4x1 push_in connector | CN17,CN5,CN4,CN18,CN1,CN2,CN11,CN12 | B2CF 3.50/04/180 SN OR BX | 8 | Weidmuller | 1277270000 | Weidmüller via Digi-Key, Conrad | https://www.conrad.de/de/p/weidmueller-buchsengehaeuse-kabel-1277270000-264-st-1952112.html | https://www.digikey.com/en/products/detail/weidmüller/1277270000/4010243
46 | M8 3pole or 4pole female | WAS | M8 FEMALE 3/4POLE 90° | 1 | Binder, Escha, Conec, etc. | Conec: 42-01427 (4-pole) 42-01419 (3-pole) | Mouser, Reichelt (4-pole only) | https://www.reichelt.de/de/en/sal-m-8-4-pin-socket-angled-conec-42-01427-p249166.html?trstct=pol_3&nbc=1 | https://www.mouser.com/_/?Keyword=42-01427 (4-pole) https://www.mouser.com/_/?Keyword=42-01427 (3-pole)
51 | PM254V-12-06-H85 | CN14,CN13 | HDR-TH_6P-P2.54-V-F-R2-C3-S2.54 |  | many |  |  | https://www.reichelt.de/de/en/pin-headers-2-54-mm-1x50-straight-mpe-087-1-050-p119891.html?&nbc=1
53 | Double layer DIP 90° white | USB_AUX | USB-A-TH_USB-M-51 | 1 | many |  |  | https://www.reichelt.de/de/en/usb-mounting-socket-typ-a-angled-print-assembly-rnd-205-00859-p253046.html?nbc=1
69 | A2541WV-2P | CN7,J1,UARDU,CN15,BOOT,J4 | HDR-TH_P2.54-H-M_A2541WV-2P |  | many |  |  | https://www.reichelt.de/de/en/pin-headers-2-54-mm-1x50-straight-mpe-087-1-050-p119891.html?&nbc=1
 | Bynav socket | U16 | HDR-TH_28P-P2-V | 1 | many |  |  | https://www.reichelt.de/de/en/sockets-2-00-mm-2x16-straight-mpe-156-3-032-p119997.html?&nbc=1

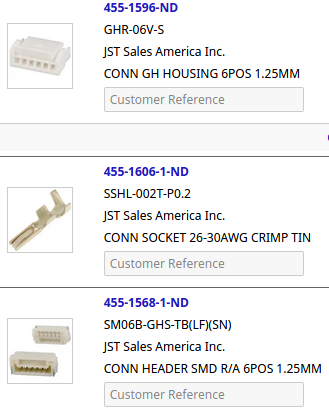
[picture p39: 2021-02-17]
central_unit/documentation/Pixhawk_cable_parts.png

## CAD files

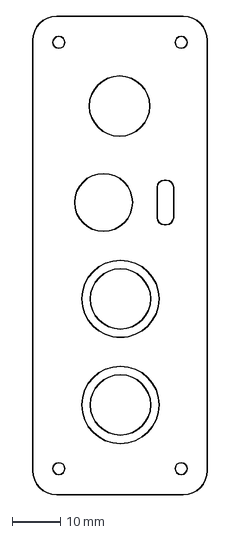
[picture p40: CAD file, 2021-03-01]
central_unit/mechanical_data/milling_left_side.DXF
36.2 x 99.2 mm

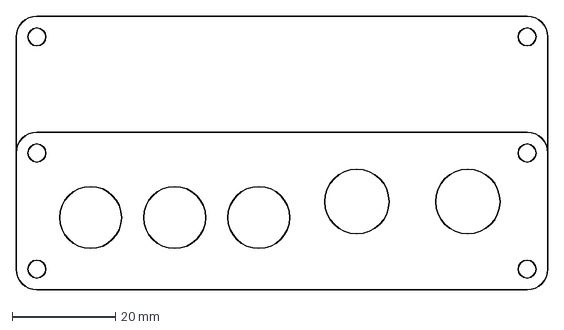
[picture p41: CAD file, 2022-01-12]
IMU_unit/mechanical_data/right_side_Hammond_1455L1601_or_1455N1601.dxf
103.0 x 53.0 mm

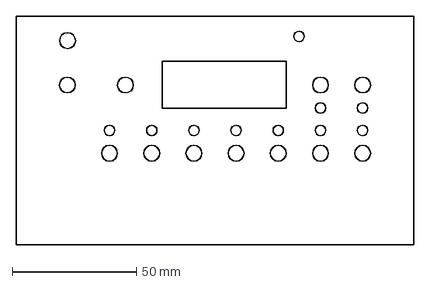
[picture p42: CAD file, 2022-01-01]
section_and_rate_control_unit/mechanical_data/Frontpanel_SectionControlUnit_7Sec.dxf
160.0 x 92.0 mm

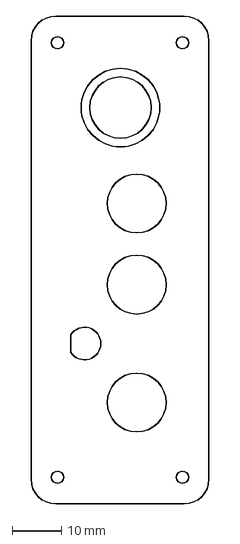
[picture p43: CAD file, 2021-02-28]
central_unit/mechanical_data/milling_right_side.DXF
36.2 x 99.2 mm

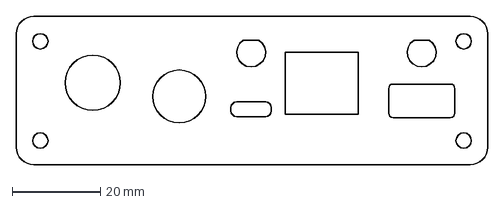
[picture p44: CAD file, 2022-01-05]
IMU_unit/mechanical_data/left_side_Hammond_1457L1602.dxf
106.9 x 33.7 mm

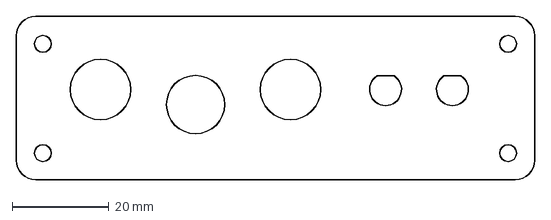
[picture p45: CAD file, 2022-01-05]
IMU_unit/mechanical_data/left_side_Hammond_1457L1602_waterproof_M12-D.dxf
106.9 x 33.7 mm

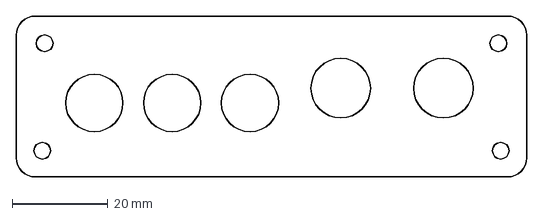
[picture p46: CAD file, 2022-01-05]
IMU_unit/mechanical_data/right_side_Hammond_1457L1602.dxf
106.9 x 33.7 mm

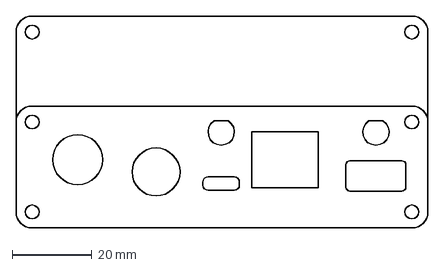
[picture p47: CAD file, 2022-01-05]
IMU_unit/mechanical_data/left_side_Hammond_1455L1601_or_1455N1601.dxf
103.0 x 53.0 mm

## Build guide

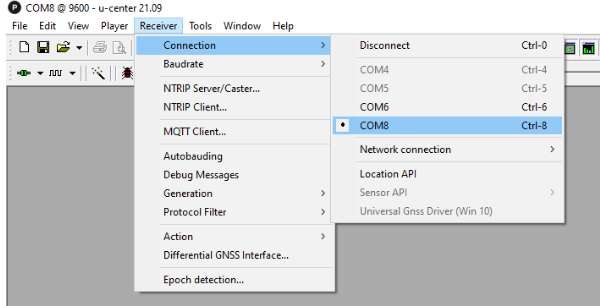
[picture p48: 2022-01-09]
central_unit_2.0/documentation/setup_Ardusimple/1st_connect_Ardusimple_to_YOUR_com_port.png

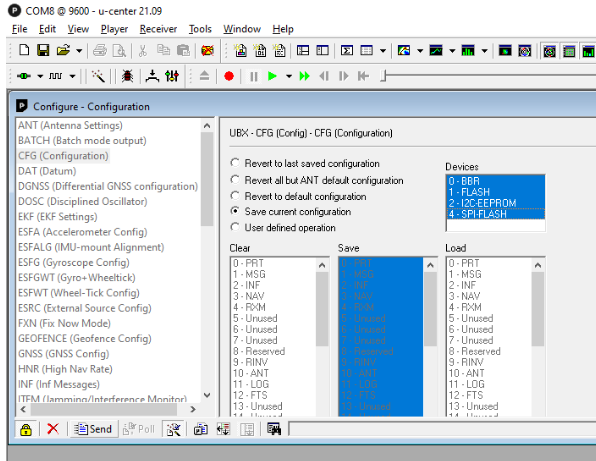
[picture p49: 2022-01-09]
central_unit_2.0/documentation/setup_Ardusimple/5th_select_Devices_and_click_Send_to_save_permanently.png

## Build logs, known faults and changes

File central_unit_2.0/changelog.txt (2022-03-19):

V2.0
- first release 
- short drain and source of Q250
- solder 2k resistor between GND and _Reset of Atmel (best is @ PRGBOOT)
- clavilux when USB is connected to Win (not on Linux for any reason); rise/disconnect pin 7 of U22 and U23
- cut A0/WAS line between Atmel and ADC; connect to current measurement line instead
- add 1k in series to LED M3
- W5500: R203=10R, R205 & R206 to C200, C215..17 added

V2.1
- R260 changed to 1k from 10k
- R263 added
- Q250 value change
- outline modified for PushIn connector
- R64 connected to 3V3 instead of 5V
- D31 removed, jumper USB_SC added
- Q14, Q15 changed to 2N7002 (lower threshold voltage)
- U800 changed to LM2904DR2G (push-pull output needed)
- A0 of Atmel used for current measurement (disengagement of motor) now
- D26 and R44 added
- D27 added (just to be very safe)
- values modified to be 24V-safe: R22, R35, R44, R51, R55, R62, R71, R71, R82, R92
- mods for W5500

V2.2
- Power Line Communication option added based on THVD8000: R83, U8a, L1, L2, C24, C25, Q16 - either place components for RS485 or for Power Line Communication (OOK modulation)
- D28, D29 added just to be very sure on ESD
- names of input signals named "Steer", "Work", text "left.." and "right.." added
- F1, F2 added
- R70, R47, R45 added (needed for ESP32-only solution)
- WorkAnalog connected to µCs (accidentially forgotten - digital input for Atmel working anyway)
- Out1 replaces D23, polarity of optocoupler output changed, D5/AuxOut to GPIO0, A0/Current to GPIO32, R78, R94, R95, Q22..Q24, _OFF deleted (motor torque switch-off is now part of Brian's Arduino code)

V2.3
- USB3 added to enable dual-RTK w/o ESP32 (all just via USB)
- R78, R79 added as protection

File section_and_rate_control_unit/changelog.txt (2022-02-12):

V1.0
- first release 
- USB lines crossed (workaround: cut both lines underneath D15; reconnect one on top and the other on bottom - see pictures in doc folder)
- additional discharge resistors for readback

V1.1 (Dec 29th, 2021)
- USB lines corrected
- R66..R69, R85..R88 added

V1.2 (Feb, 12th, 2022)
- two-wire powerlink bus option added: U7, R90, R91, C26, C27, L2, L3, D17..D20
- R92, R93 added

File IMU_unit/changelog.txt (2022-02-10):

V1.0
- first release 
- Rx and Tx swapped
- programming of bootloader: remove C55
- access to Rx and Tx for stardard-Arduino programming: best at LEDs

V1.1
- bugfix Rx/Tx
- R5, R9 added
- Testpoints on Rx and Tx added for programming

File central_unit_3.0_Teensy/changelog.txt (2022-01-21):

V3.0
- first release (untested)
- H9: no perfect fit: use copper wires (3 wires for +, D+ and D- necessary only)
- add 1k resistor in series to LED "M3"

V3.1
- H9 shifted 1mm to the left
- outline modified for PushIn connector
- D30 and R44 added
- values modified to be 24V-safe: R35, R44, R51
- D32, D33, D34 added (additional ESD protection)
- input signals named "Work", "Steer" and "Remote"; pinning like CU2

V3.2
- Power Line Communication option added based on THVD8000: R83, U8a, L1, L2, C24, C25, Q16 - either place components for RS485 or for Power Line Communication (OOK modulation)
- F1, F2 added

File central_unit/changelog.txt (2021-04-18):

V1.3
- first prototype

V1.4
- U14 added to support 6/2 valves
- R103 and R105 added to decouple Atmel and ESP32

V1.5
- Pixhawk connector to Ardusimple added
- Option switching of M12-GNSS via jumpers (R43, R46, R100, R101 deleted)

V1.6
- Bugfix USB-C: pulldown resistors R43 and R46 added, Q7 turned

V1.7
- CN3 added
- M8/M12 shifted by 3.4mm overall
- J5, R97 removed (never needed)
- C1: 1uF => 0.1uF (just because the datasheet tells so - no malfunction known)
- C44 => R100 (otherwise the SMPS doesn't switch off)
- Q9, Q10 added to minimize influence for non-buffered WASs

V1.8
- pinning of ESP32 set as https://github.com/mtz8302/AOG_Autosteer_ESP32
- USB-C receptacles THT now to ease soldering
- necessary pin headers are part of the JLCPCB BOM now

V1.9
- bugfix Q8: Gate was on the wrong pin
- Q12 added to minimize braking effect in H bridge

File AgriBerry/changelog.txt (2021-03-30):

V1.0
- first prototype

V1.1
- some mechanical mods

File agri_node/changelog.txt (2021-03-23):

V1.0
- first prototype

V1.1
- SCLK and _CS @ 74HC595 swapped
- H11, H12 moved
- default level for DI3 inverted (due to bootstrap option of that pin; has to be idle @ startup

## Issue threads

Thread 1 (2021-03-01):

V1.3: Extra milling for M8

GormR, 2021-03-01:

GormR, 2021-03-01:
fixed with V1.5

Closed 2021-03-01.

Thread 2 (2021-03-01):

if using the M8/M12 connectors and suggested aluminum housing: housing has to be shortend

GormR, 2021-03-01:
short it by 3.4mm

GormR, 2021-03-01:
fixed with V1.8

Closed 2021-03-01.

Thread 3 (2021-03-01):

no data communication when using USB-C

GormR, 2021-03-01:
- no charging and communication in parallel
- no communication

GormR, 2021-03-01:
workaround communication: use two 5.1k resistors between CC1, CC2 to 0V as shown in https://agopengps.discourse.group/t/smd-pcb-project-for-an-all-in-one-compact-pcb-for-aog-qog/3640/163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

GormR, 2021-03-01:
correction of first issue will lead to a new piggyback PCB, but no mods needed for the main PCB

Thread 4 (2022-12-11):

compiling problems

ckarall, 2022-12-11:
Hello,
can somebody help me:
"
Autosteer_Teensy_UDP_v5_0: In function 'void loop()':

Autosteer_Teensy_UDP_v5_0:793: error: 'calcSteeringPID' was not declared in this scope

       calcSteeringPID();  //do the pid

                       ^

Autosteer_Teensy_UDP_v5_0:794: error: 'motorDrive' was not declared in this scope

       motorDrive();       //out to motors the pwm value

                  ^

Autosteer_Teensy_UDP_v5_0:814: error: 'motorDrive' was not declared in this scope

       motorDrive(); //out to motors the pwm value

                  ^

Autosteer_Teensy_UDP_v5_0:429: warning: unused variable 'steerLeft'

   int steerLeft = 0;

       ^
"

I have included following files:
[Autosteer_Teensy_UDP_v5_0.ino]
[BNO08x_AOG.cpp]
[BNO08x_AOG.h]
[FUSB302.h]
tcpm.h
tcpm_driver.cpp
tcpm_driver.h
usb_pd.h
usb_pd_driver.h
usb_pd_tcpm.h
zADS1115.cpp
zADS1115.h

should I include also the following files:
[FUSB302.c]
[platform.h]
[usb_pd_driver.c]
[usb_pd_policy.c]
[usb_pd_protocol.c]

in which folder I have to put those files?

ckarall, 2023-01-08:
.

Closed 2023-01-08.

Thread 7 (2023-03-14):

EasyEDA json files won't open in EasyEDA

m-elias, 2023-03-14:
Either I can't figure this out or something is wrong with the EasyEDA json files. When I try to open them in EasyEDA Standard desktop v6.5.22, it does nothing, just goes back to my previous view. I have Section Control v1.1 PCB that I'd like to get the design files to study.

m-elias, 2023-03-14:
I just now found the oshwlab link and was able to clone that to my account. Thanks for sharing this project!
https://oshwlab.com/GoRoNb/aog_io-box_copy

Closed 2023-03-14.

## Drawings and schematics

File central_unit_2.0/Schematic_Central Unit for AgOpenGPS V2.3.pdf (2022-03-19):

# RS485 / ModbusRTU I2C external

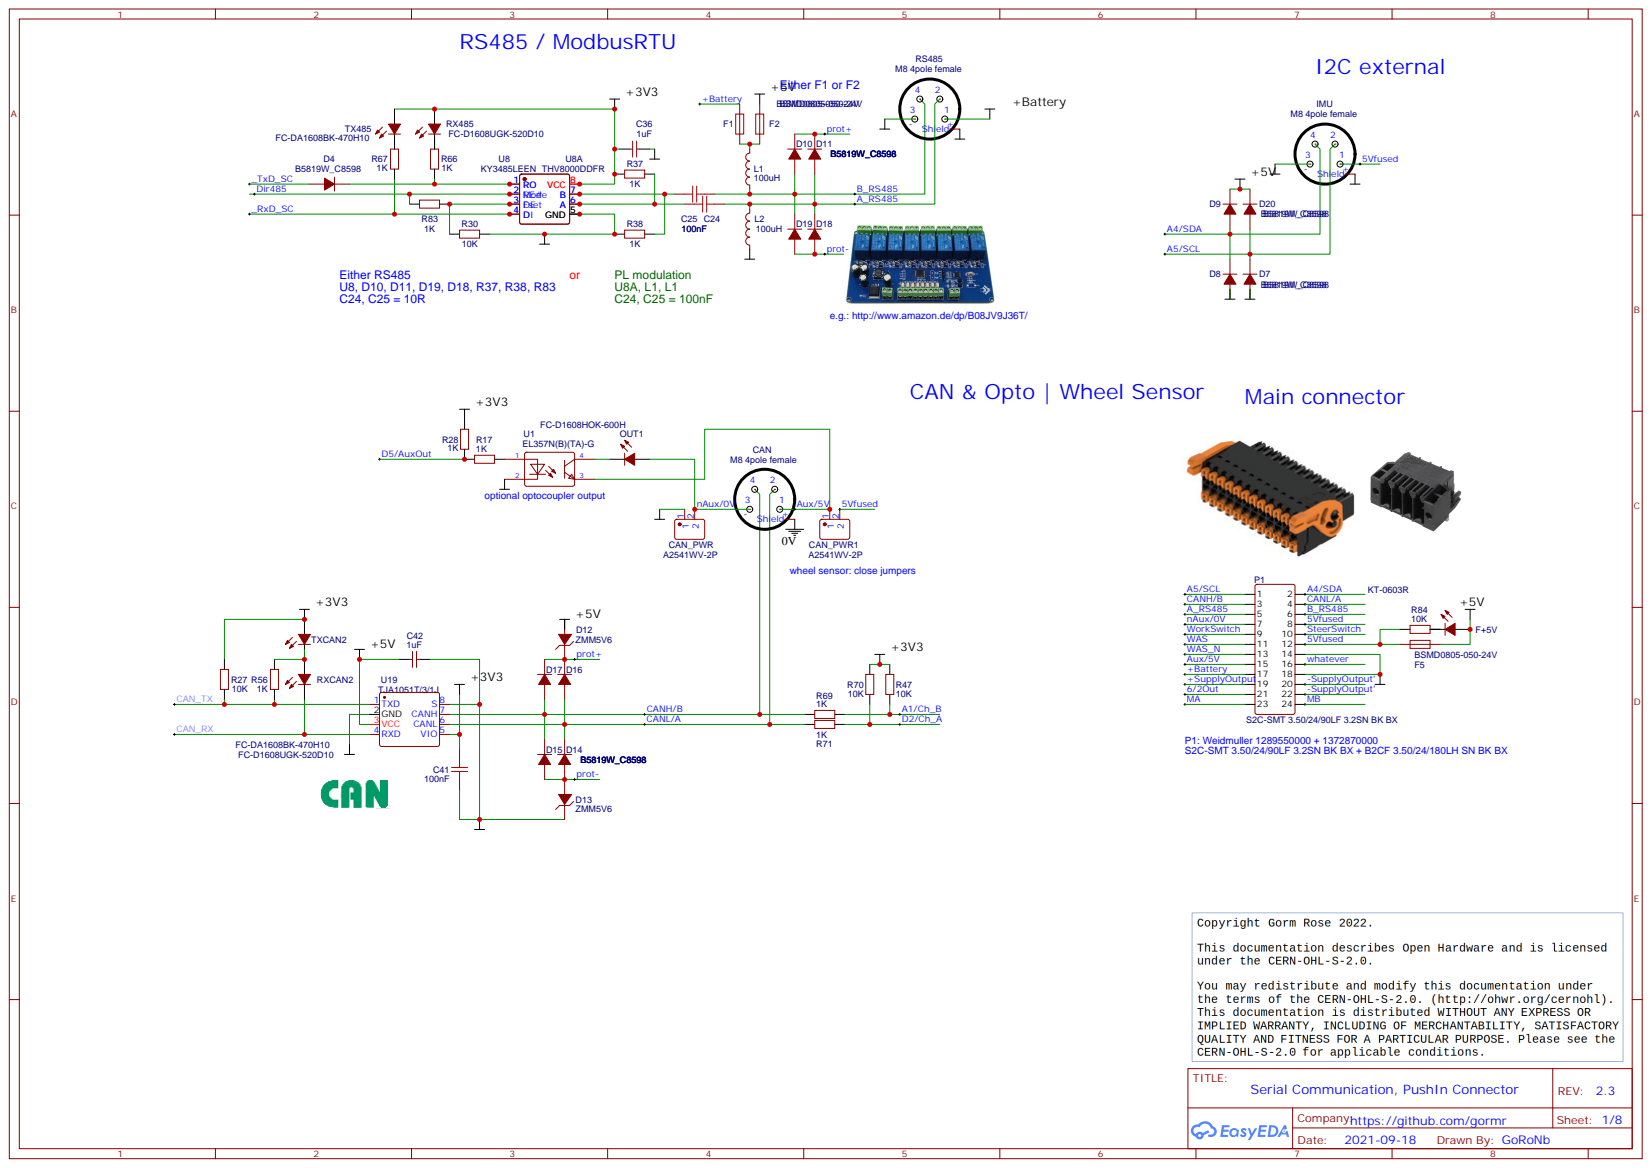
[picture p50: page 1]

e.g.: http://www.amazon.de/dp/B08JV9J36T/

CAN & Opto | Wheel Sensor

P1: Weidmuller 1289550000 + 1372870000
S2C-SMT 3.50/24/90LF 3.2SN BK BX + B2CF 3.50/24/180LH SN BK BX

Company:https://github.com/gormr

# ADC

# Wheel Angle Sensor

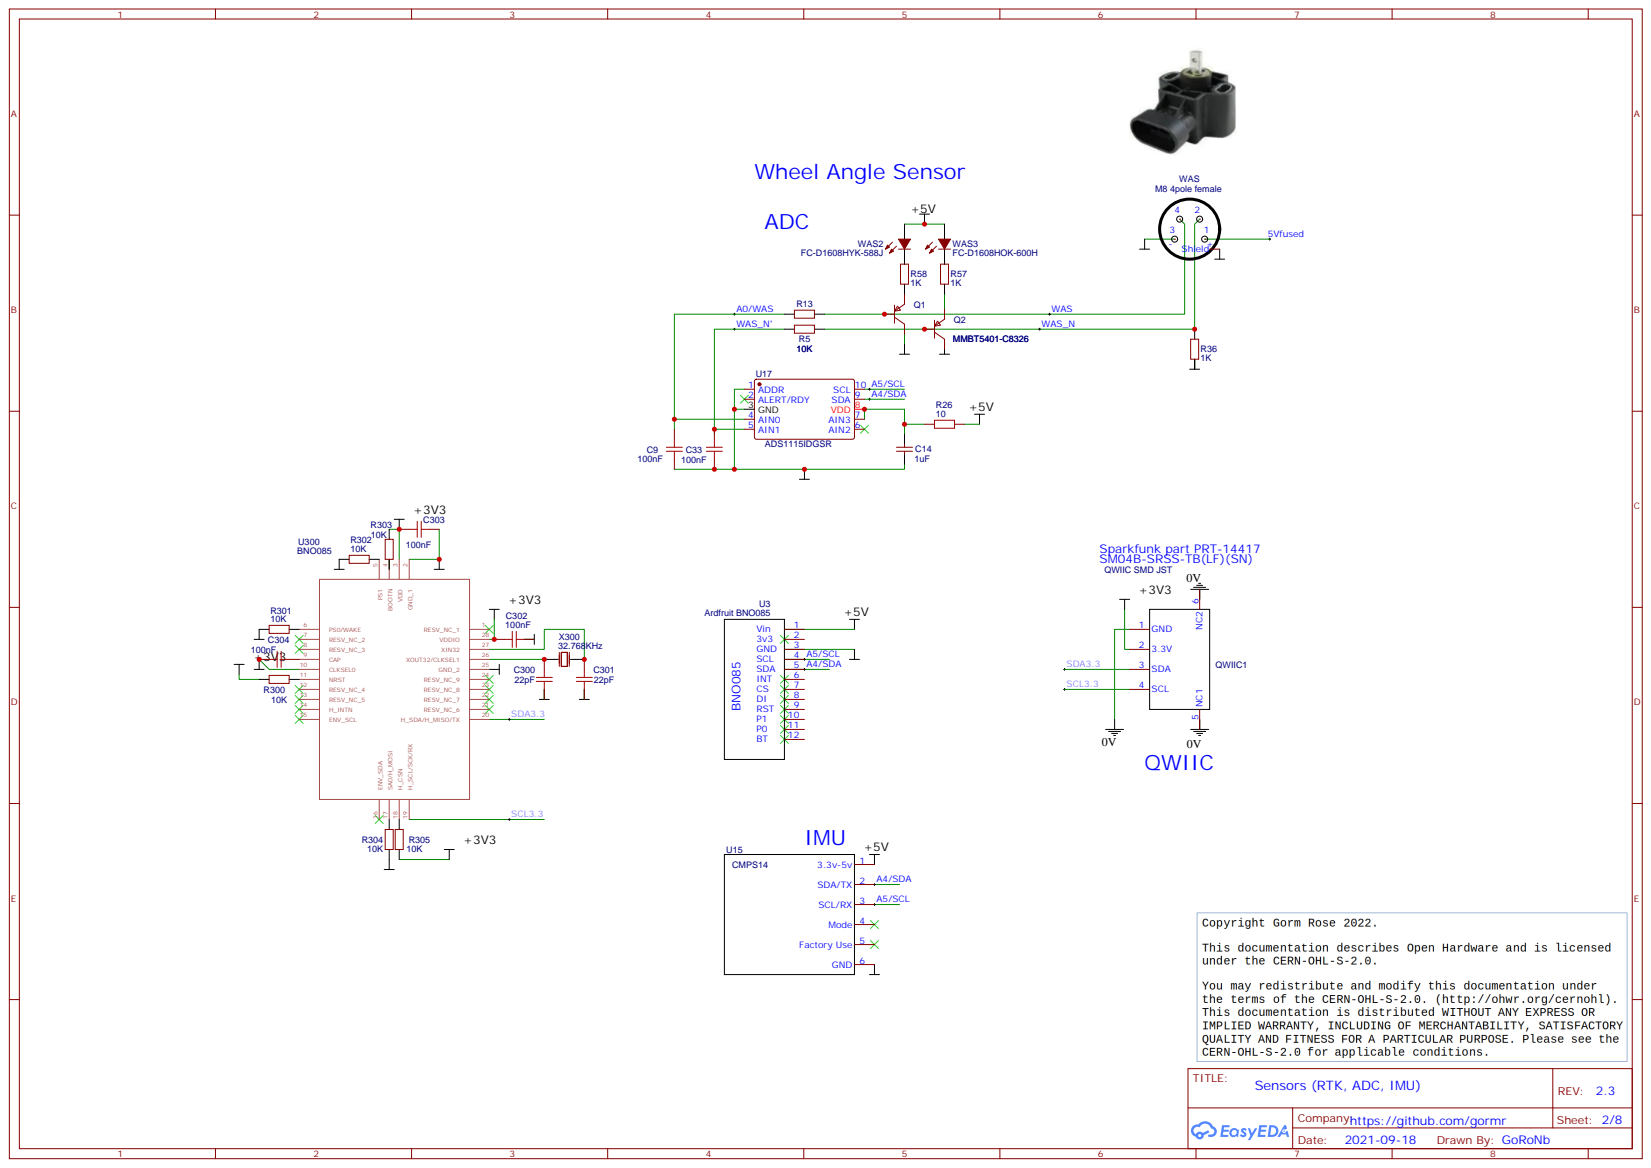
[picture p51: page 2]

Sparkfunk part PRT-14417
SM04B-SRSS-TB(LF)(SN)
QWIIC SMD JST

## LED colors: white: power

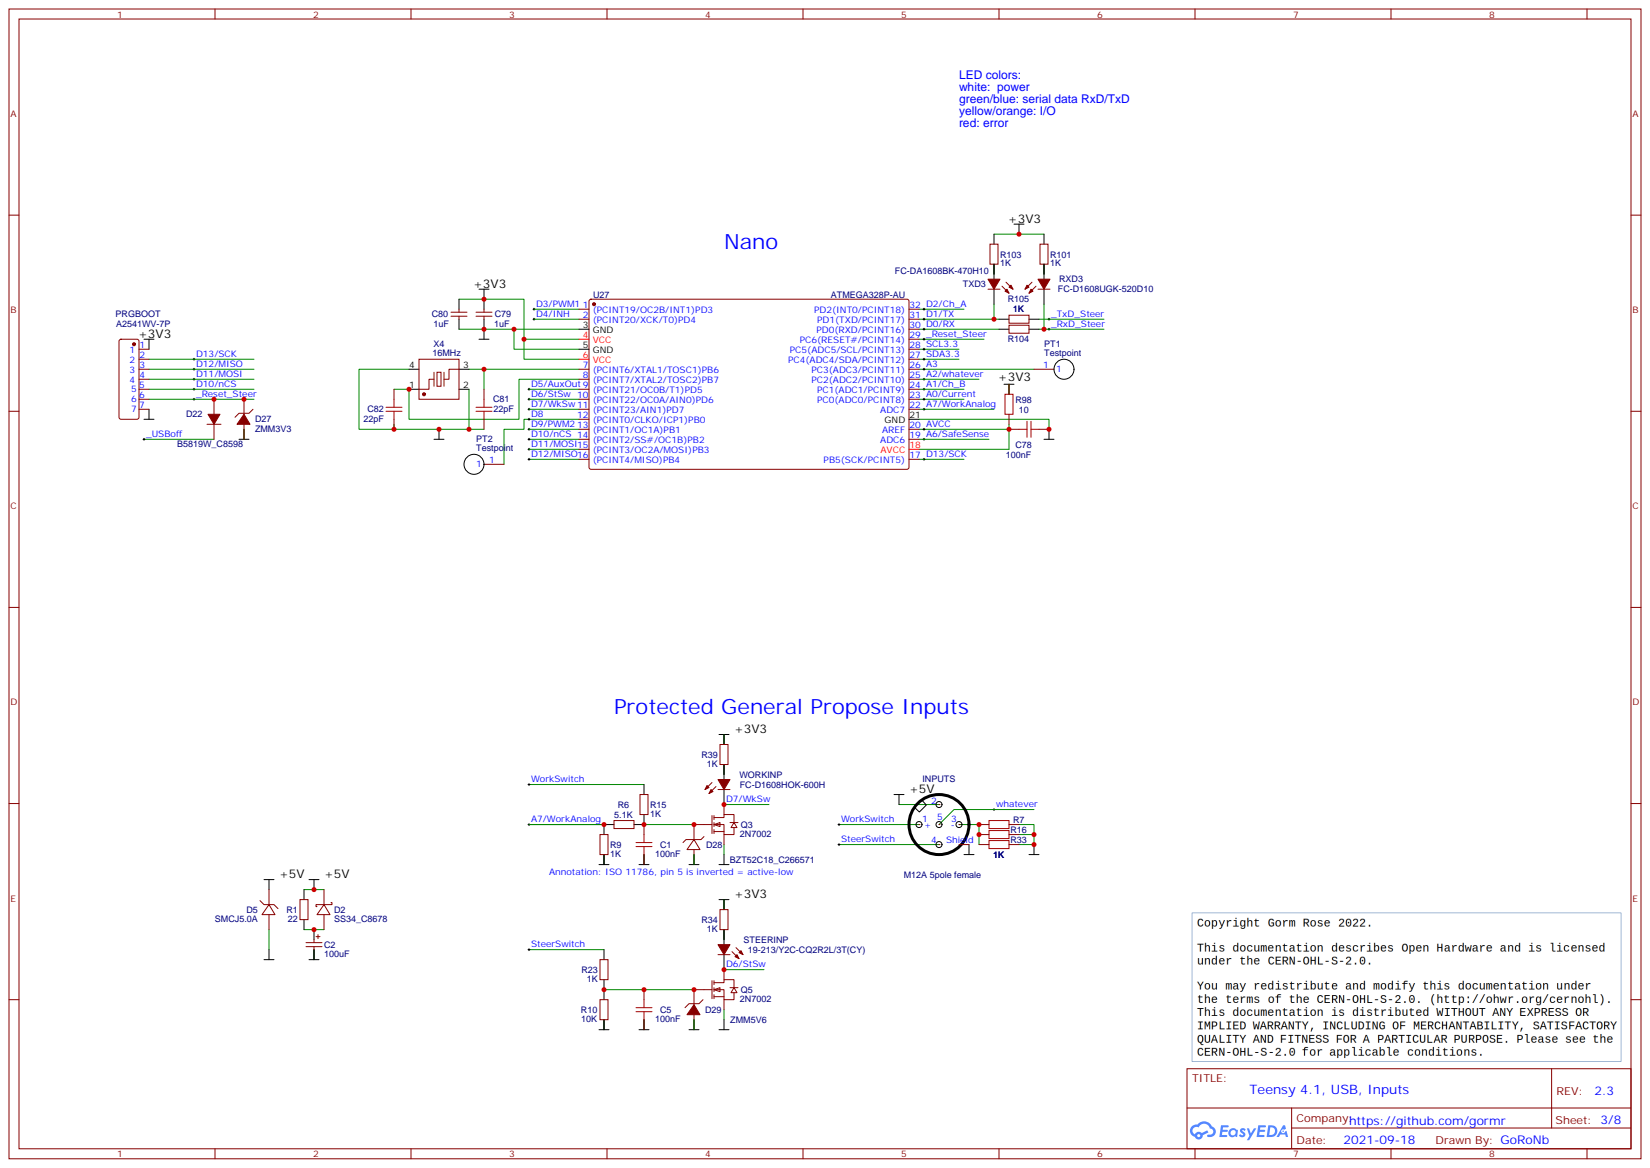
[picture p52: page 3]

green/blue: serial data RxD/TxD
yellow/orange: I/O
red: error

Protected General Propose Inputs

Annotation: ISO 11786, pin 5 is inverted = active-low

## LED colors: white: power

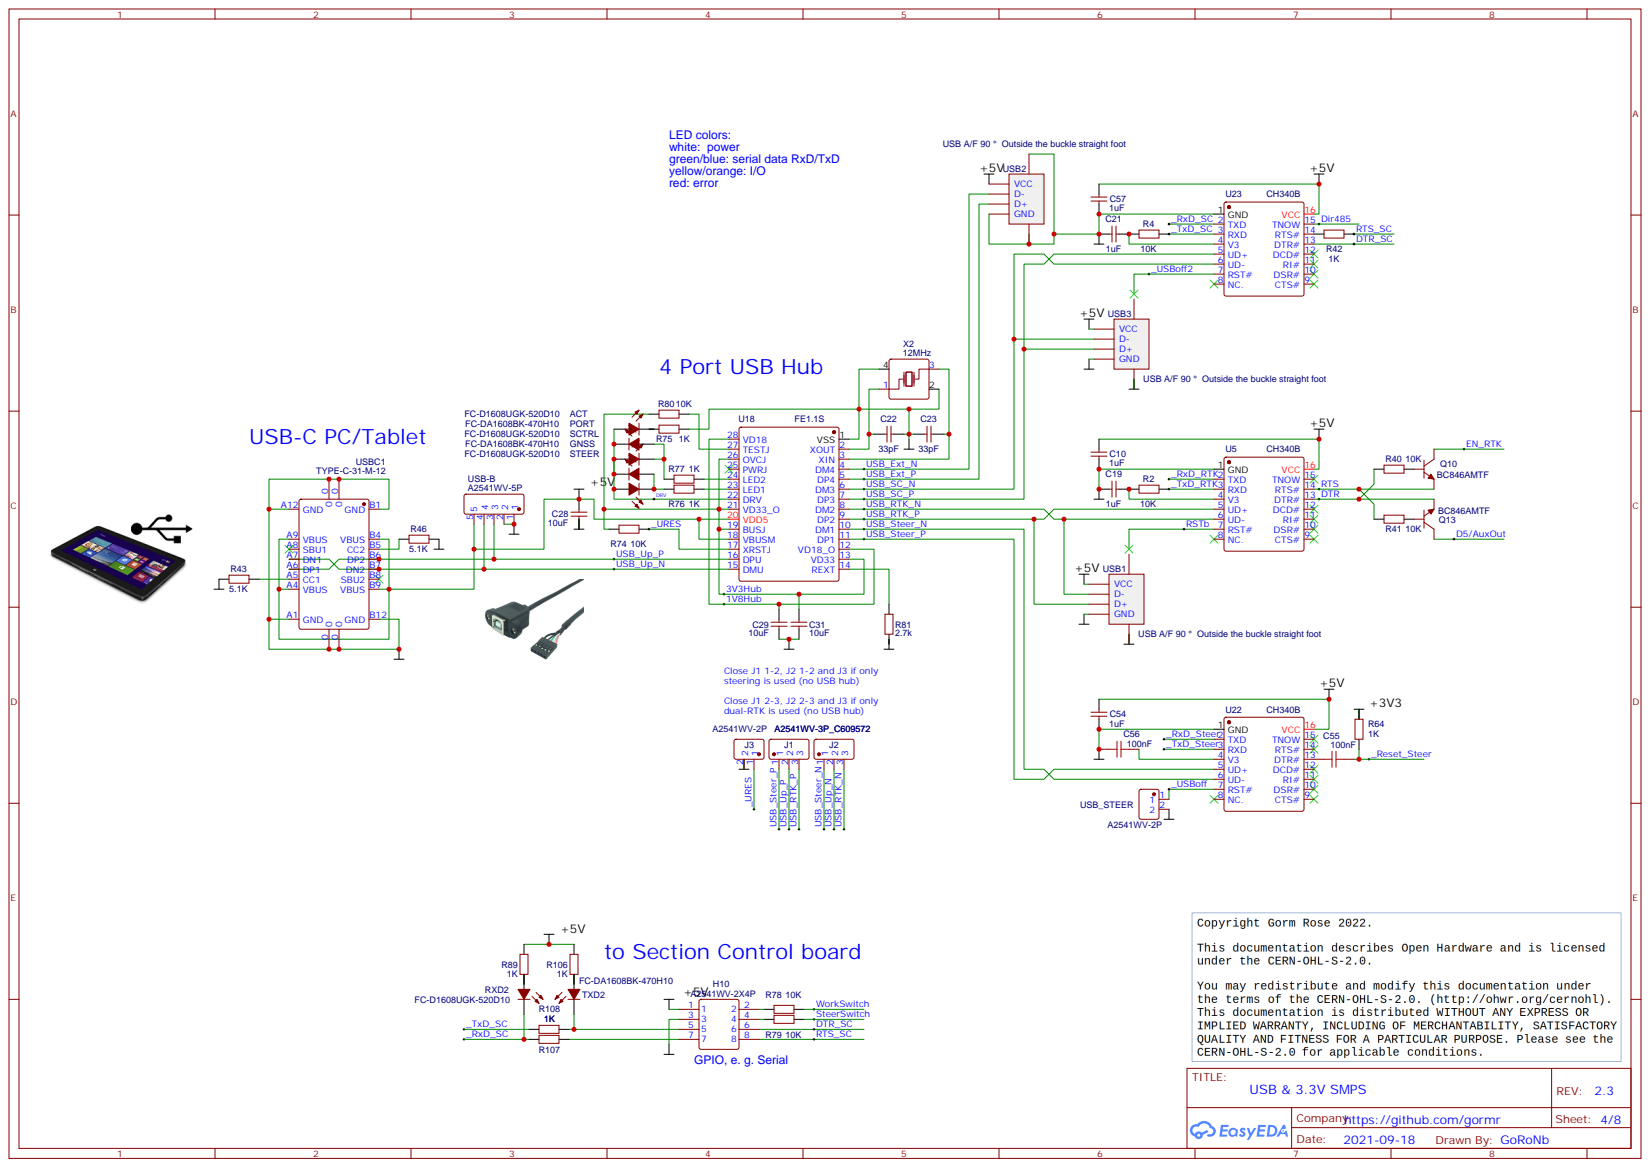
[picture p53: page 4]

green/blue: serial data RxD/TxD
yellow/orange: I/O
red: error

REXT 14 DMU 15 DPU 16 XRSTJ 17 VBUSM 18 BUSJ 19 VDD5 20 VD33_O 21 DRV 22 LED1 23 LED2 24 PWRJ 25 OVCJ 26 TESTJ 27 VD18 28

Close J1 1-2, J2 1-2 and J3 if only
steering is used (no USB hub)
Close J1 2-3, J2 2-3 and J3 if only
dual-RTK is used (no USB hub)

to Section Control board

# Ardusimple Onboard Module(s)

+3V3

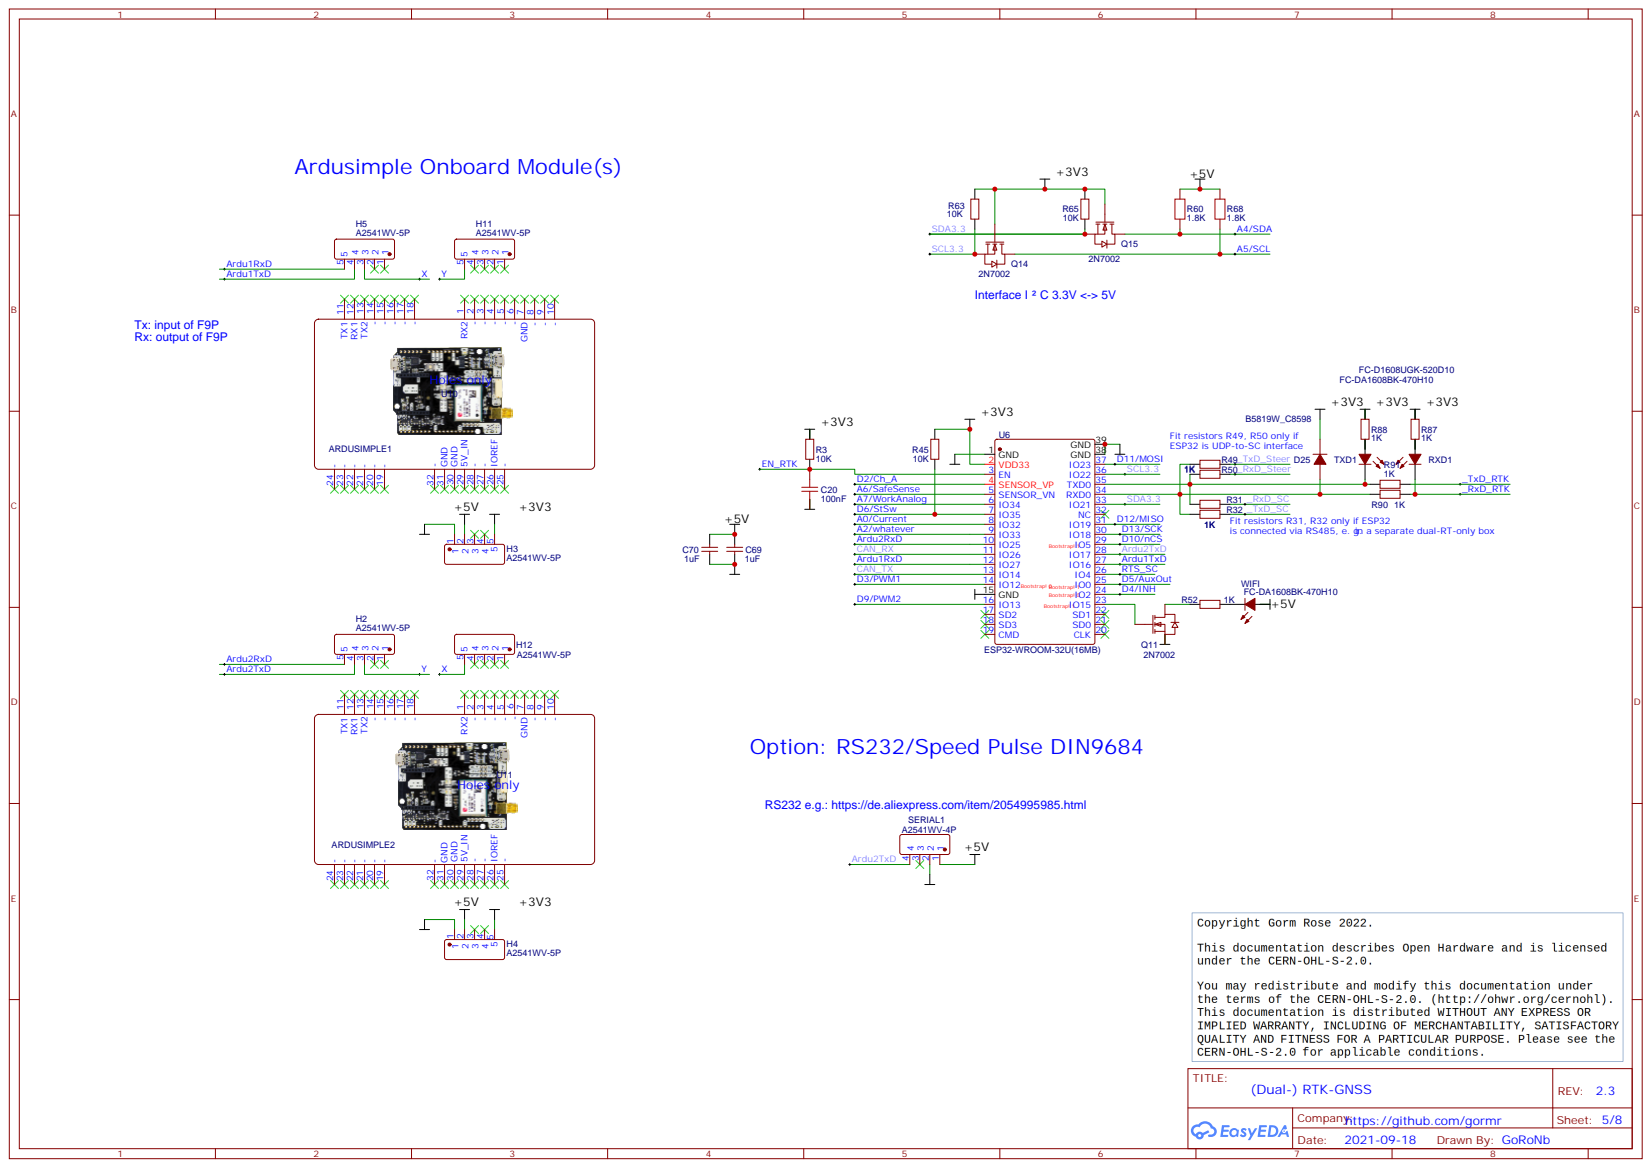
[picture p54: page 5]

Fit resistors R49, R50 only if
ESP32 is UDP-to-SC interface

in a separate dual-RT-only box

RS232 e.g.: https://de.aliexpress.com/item/2054995985.html

## acc. ISO13850

# H Bridge

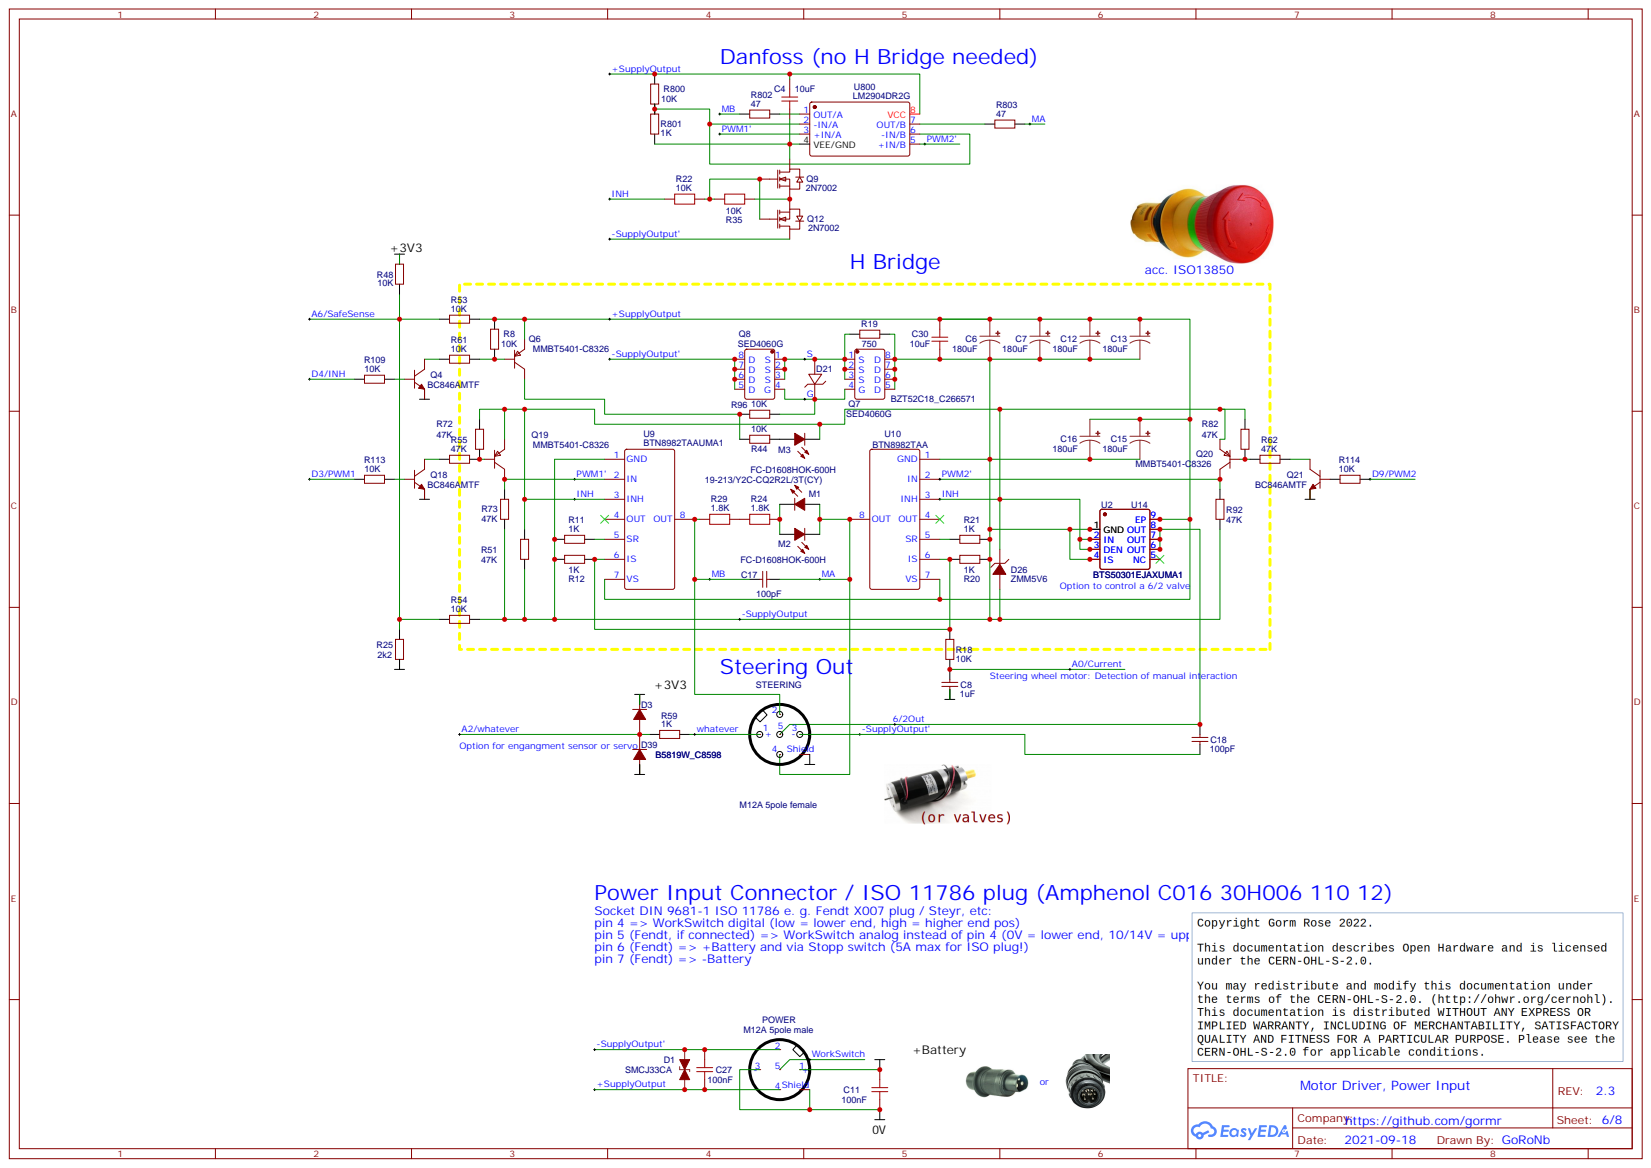
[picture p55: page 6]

Danfoss (no H Bridge needed)

Option to control a 6/2 valve

A2/whatever
Option for engangment sensor or servo

Power Input Connector / ISO 11786 plug (Amphenol C016 30H006 110 12)
Socket DIN 9681-1 ISO 11786 e. g. Fendt X007 plug / Steyr, etc:
pin 4 => WorkSwitch digital (low = lower end, high = higher end pos)
pin 5 (Fendt, if connected) => WorkSwitch analog instead of pin 4 (0V = lower end, 10/14V = upper end pos)
pin 6 (Fendt) => +Battery and via Stopp switch (5A max for ISO plug!)
pin 7 (Fendt) => -Battery

# Option: Ethernet

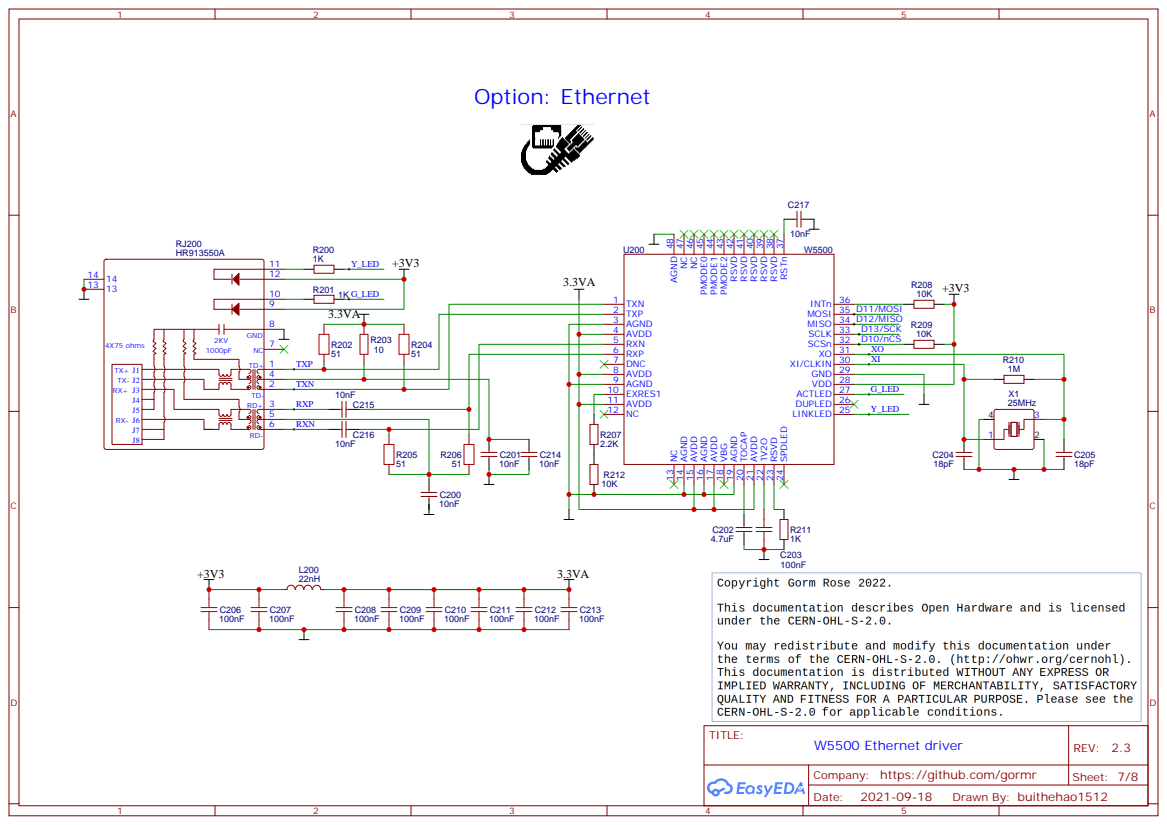
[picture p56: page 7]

LINKLED 25 DUPLED 26 ACTLED 27 VDD 28 GND 29 XI/CLKIN 30 XO 31 SCSn 32 SCLK 33 MISO 34 MOSI 35 INTn 36

RSTn 37 RSVD 38 RSVD 39 RSVD 40 RSVD 41 RSVD 42 PMODE2 43 PMODE1 44 PMODE0 45 NC 46 NC 47 AGND 48

Company: https://github.com/gormr

+Vin | +5V

## +Battery

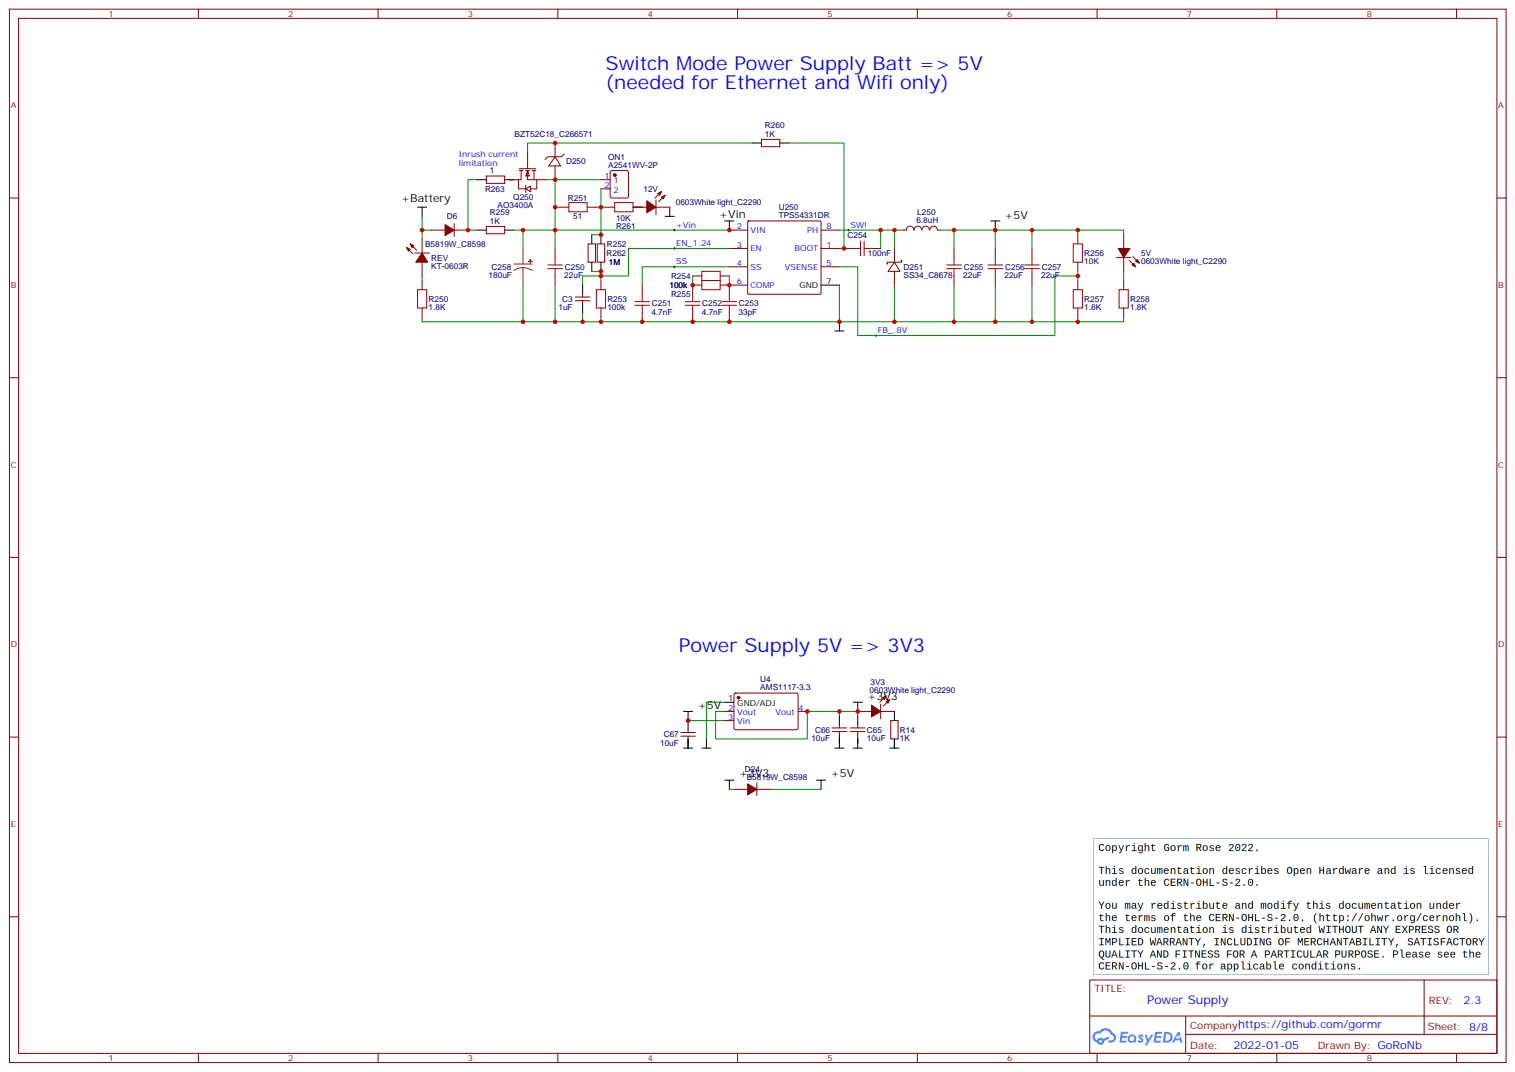
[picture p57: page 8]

Switch Mode Power Supply Batt => 5V
(needed for Ethernet and Wifi only)

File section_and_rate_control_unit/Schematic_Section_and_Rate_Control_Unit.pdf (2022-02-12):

# USB-C PC/Tablet

## LED colors:

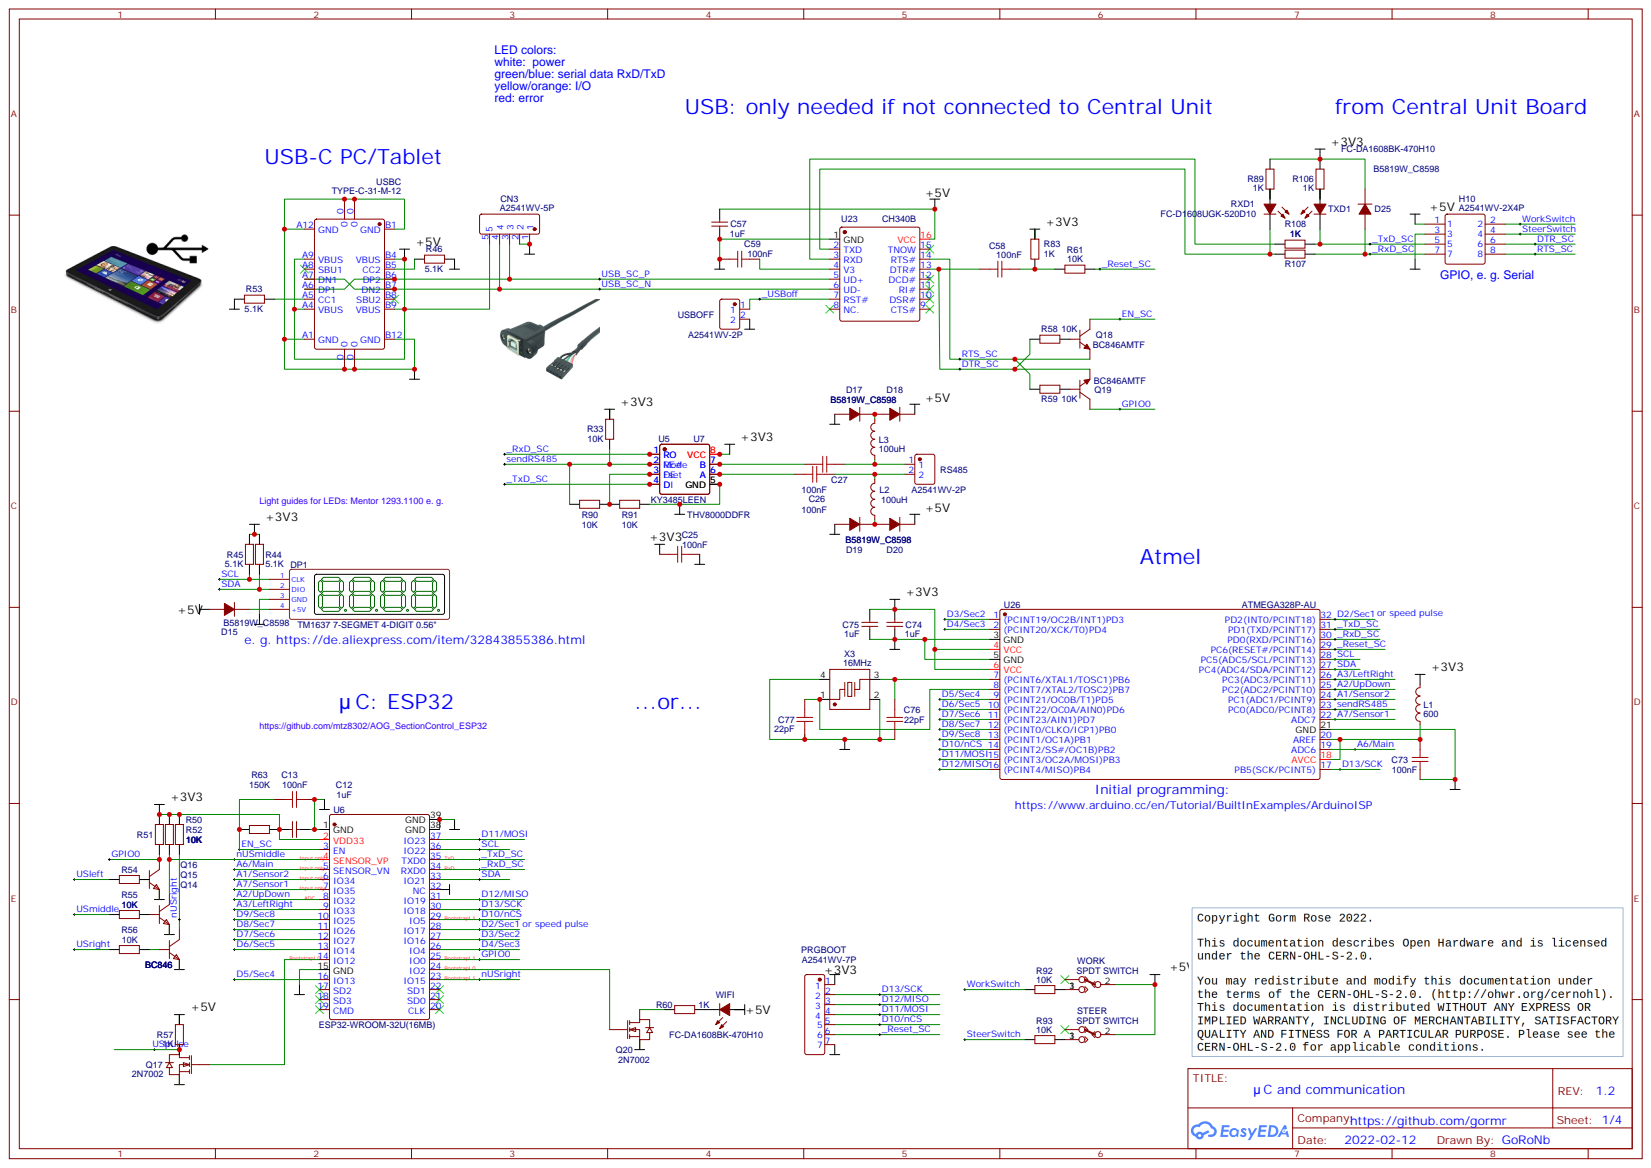
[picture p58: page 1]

white: power
green/blue: serial data RxD/TxD
yellow/orange: I/O
red: error

USB: only needed if not connected to Central Unit

from Central Unit Board

DSR# 10 RI# 11 DCD# 12 DTR# 13 RTS# 14 TNOW 15 VCC 16

e. g. https://de.aliexpress.com/item/32843855386.html

https://www.arduino.cc/en/Tutorial/BuiltInExamples/ArduinoISP

Company:https://github.com/gormr

# General options

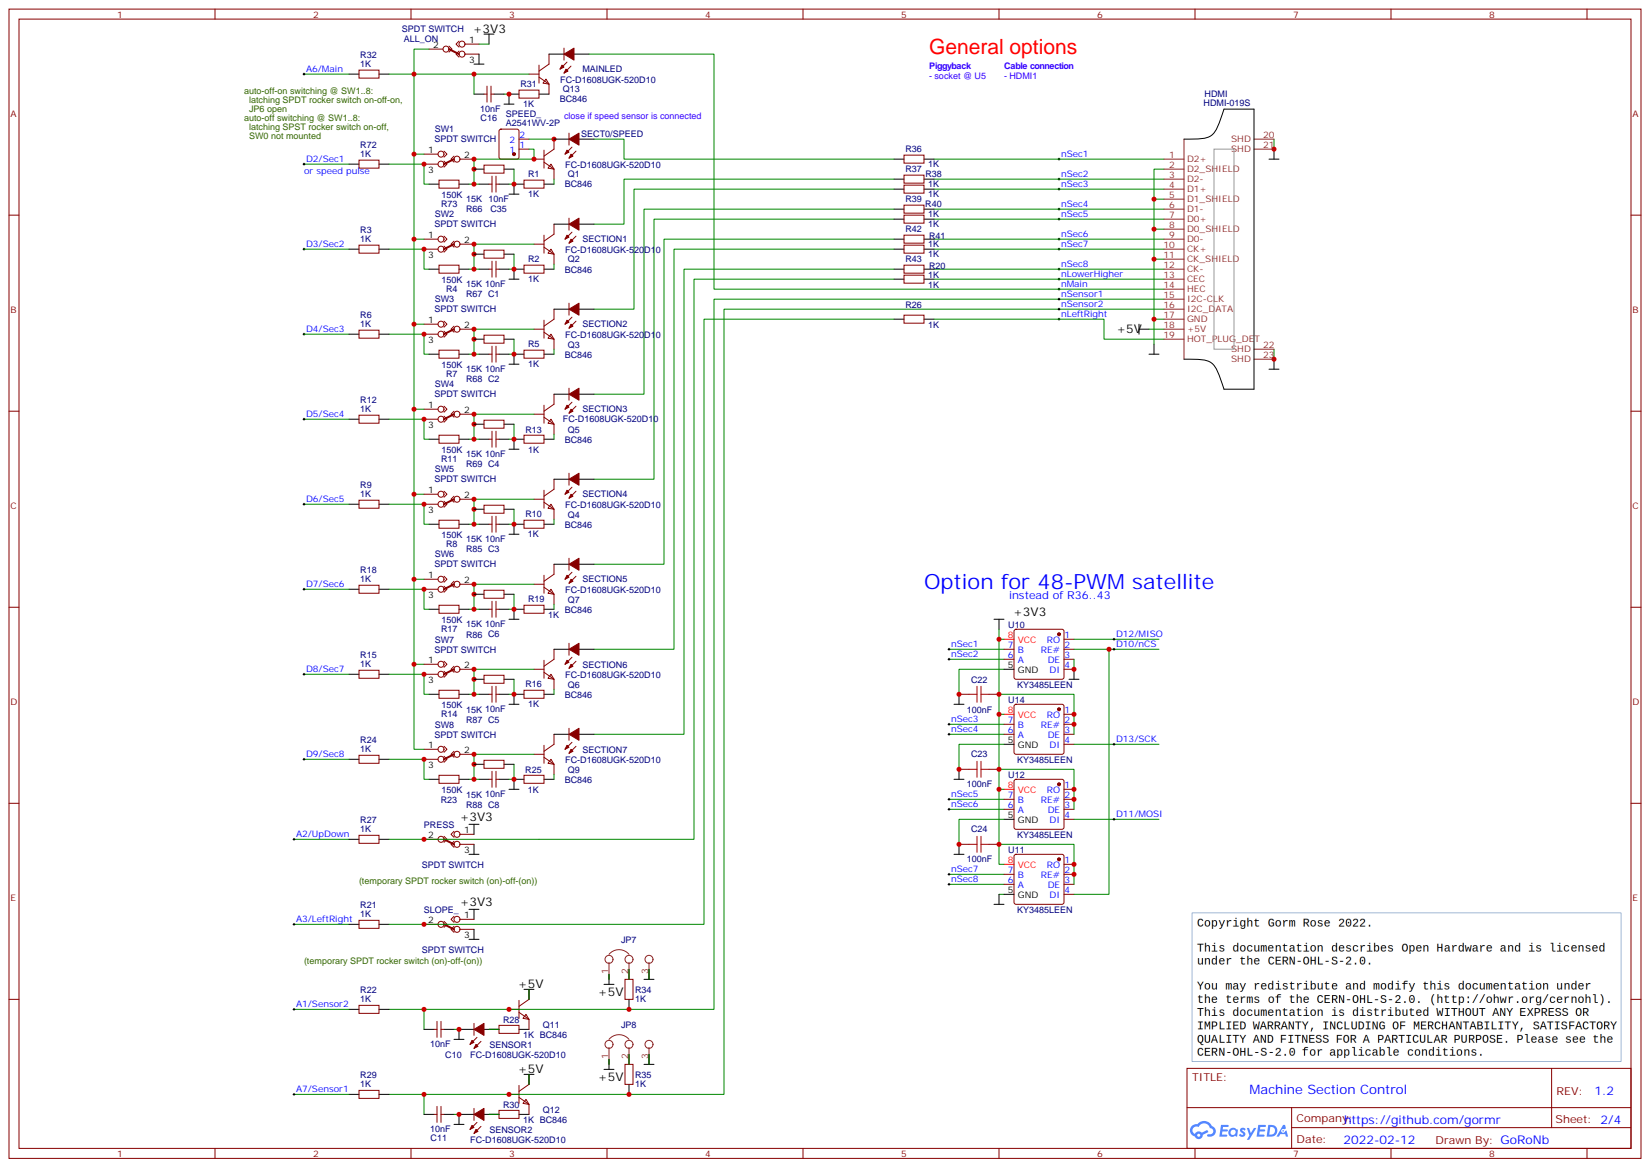
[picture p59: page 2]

auto-off-on switching @ SW1..8:
latching SPDT rocker switch on-off-on,
JP6 open
auto-off switching @ SW1..8:
latching SPST rocker switch on-off,
SW0 not mounted

Option for 48-PWM satellite

(temporary SPDT rocker switch (on)-off-(on))

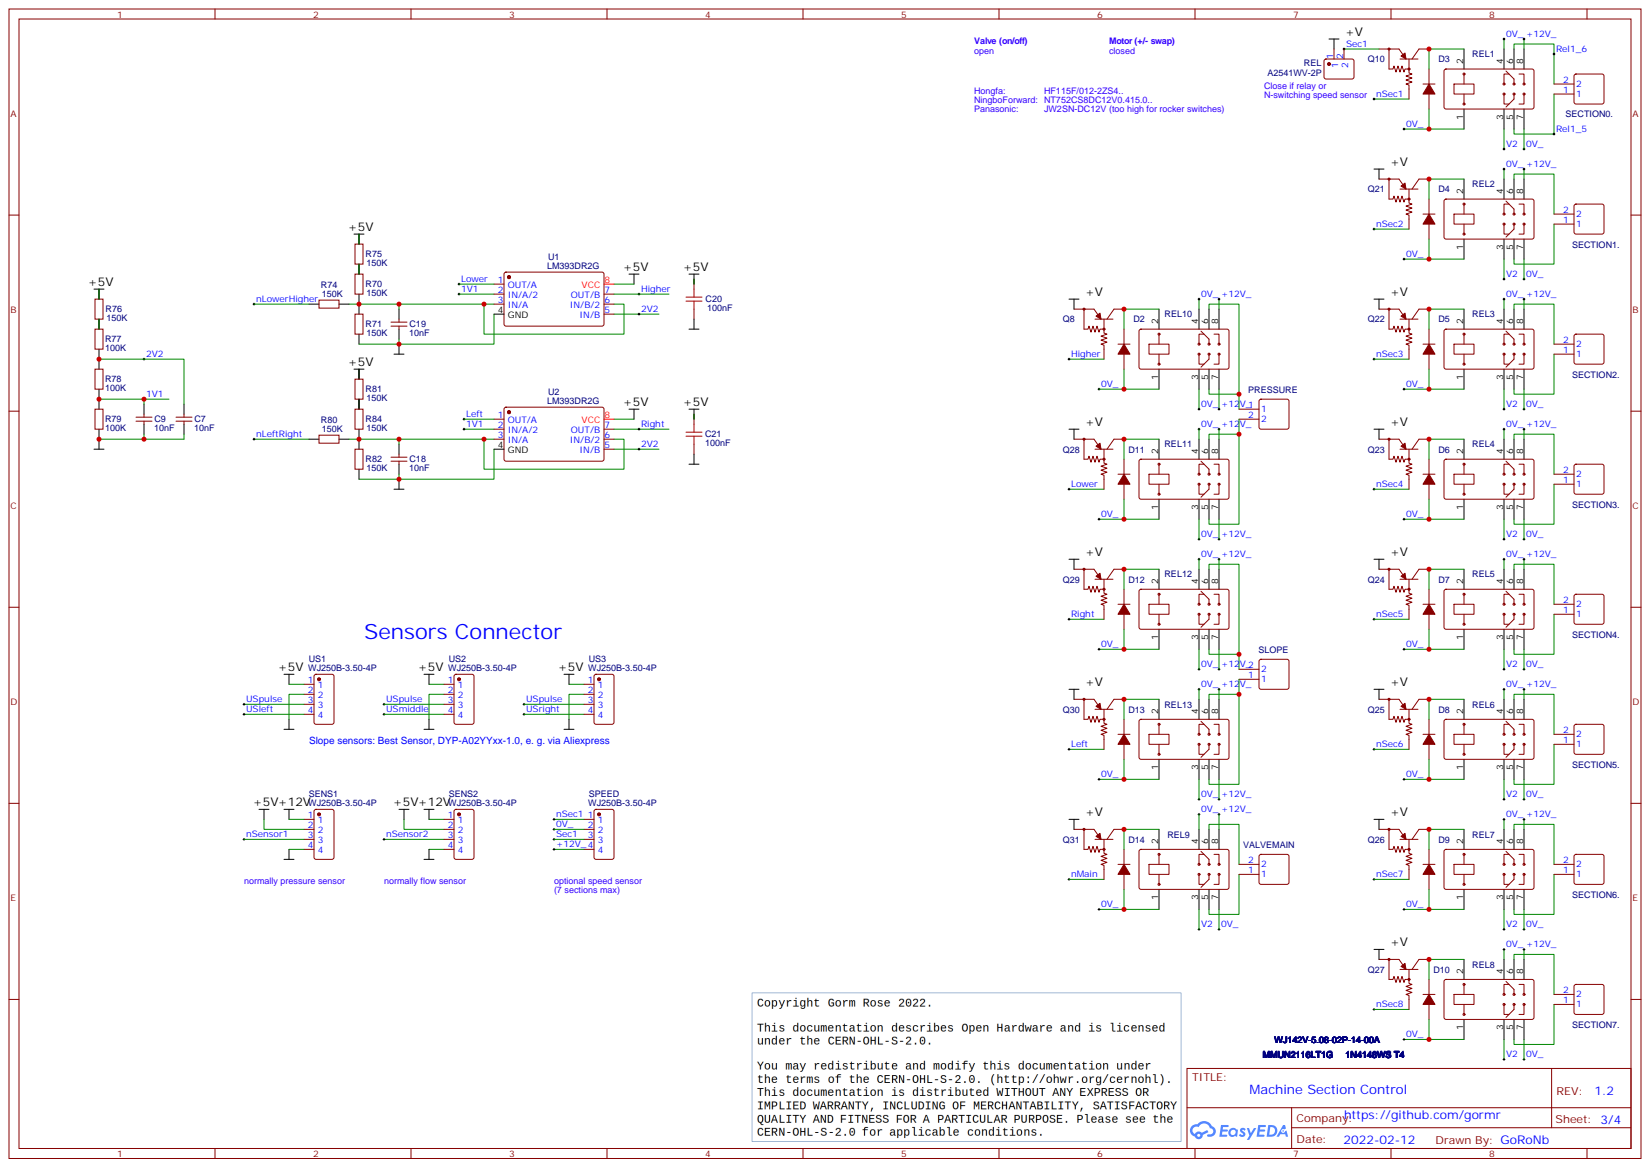
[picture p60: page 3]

Close if relay or
N-switching speed sensor

# Switch Mode Power Supply Batt => 5V (needed for Ethernet and Wifi only)

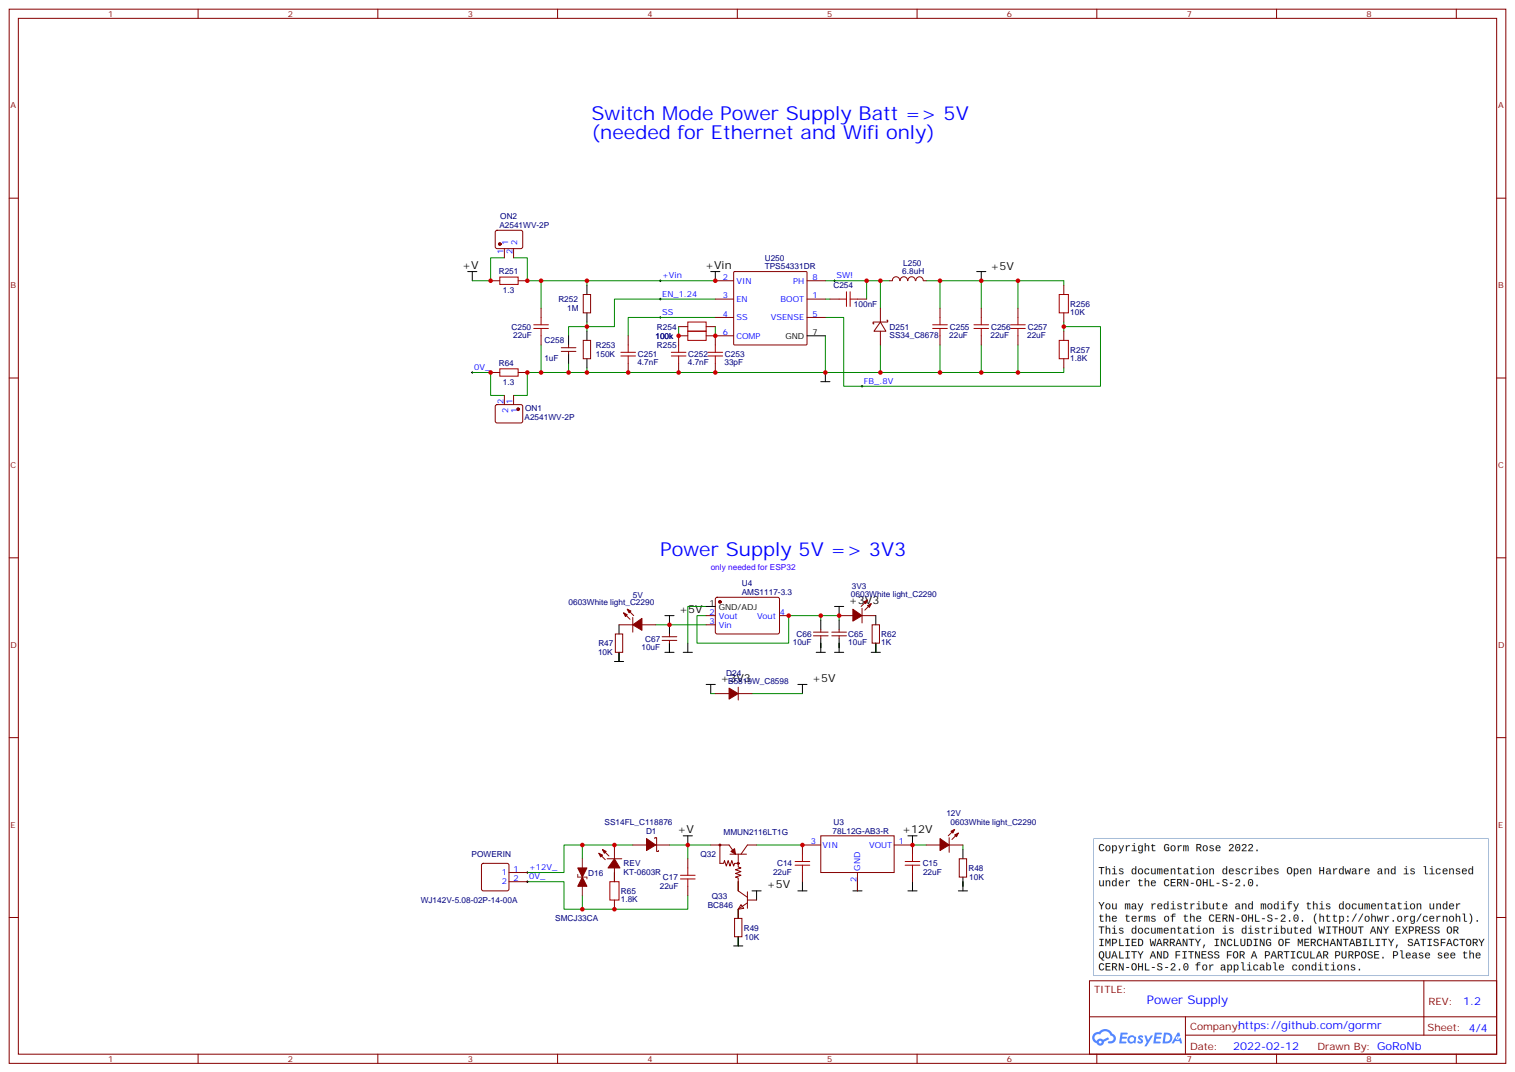
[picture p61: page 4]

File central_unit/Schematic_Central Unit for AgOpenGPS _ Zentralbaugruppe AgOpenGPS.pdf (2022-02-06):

# Roof Top Unit Connector

+5V


USB-C PC/Tablet USB-C Charger/GP

DC/AUX KH-TYPE-C-16P
VBUS A9 SUB1 A8 DN1 A7 DP1 A6 CC1 A5 VBUS A4

LED colors:
white: power
green/blue: serial data RxD/TxD
yellow/orange: I/O
red: error

2 jumpers to the left: USB on M12
2 jumpers to the right: I C on M12

GND
2 USB Options for Modbus RTU, CAN, etc.

REXT 14 DMU 15 DPU 16 XRSTJ 17 VBUSM 18 BUSJ 19 VDD5 20 VD33_O 21 DRV 22 LED1 23 LED2 24 PWRJ 25 OVCJ 26 TESTJ 27 VD18 28

Company: https://github.com/gormr

+5V

+5V


Set jumper on H1 2-3 when using ESP32

Firmware: https://github.com/mtz8302/AOG_Autosteer_ESP32

DSR# 10 RI# 11 DCD# 12 DTR# 13 RTS# 14 TNOW 15 VCC 16

Cut CLKOUT before connecting!

Close if using an external switch Close for 6/2 valve

4x1 push_in connector
Protected General Propose Inputs

Option for engangment sensor or servo

Power Input Connector / ISO 11786 plug (Amphenol C016 30H006 110 12)
Socket DIN 9681-1 ISO 11786 e. g. Fendt X007 plug / Steyr, etc:
pin 4 => WorkSwitch digital (low = lower end, high = higher end pos)
pin 5 (Fendt, if connected) => WorkSwitch analog instead of pin 4 (0V = lower end, 10/14V = upper end pos)
pin 6 (Fendt) => +Battery and via Stopp switch (5A max for ISO plug!)
pin 7 (Fendt) => -Battery

# PIO0_28/SPIFI_IO2 44 VBAT 45

# CANtact


GND
DNP R83 for MSC
Populate for DFU
https://cantact.io/cantact-pro/users-guide.html

## Holes only

+5V +5V


BM06B-GHS-TBT(LF)(SN)

DSR# 10 RI# 11 DCD# 12 DTR# 13 RTS# 14 TNOW 15 VCC 16

QWIIC SMD JST
SM04B-SRSS-TB(LF)(SN)
Sparkfunk part PRT-14417

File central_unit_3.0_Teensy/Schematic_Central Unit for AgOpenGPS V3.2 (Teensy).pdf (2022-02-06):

# H Bridge

# Danfoss (no H Bridge needed)


Option to control a 6/2 valve

whatever
Option for engangment sensor or servo

Power Input Connector / ISO 11786 plug (Amphenol C016 30H006 110 12)
Socket DIN 9681-1 ISO 11786 e. g. Fendt X007 plug / Steyr, etc:
pin 4 => WorkSwitch digital (low = lower end, high = higher end pos)
pin 5 (Fendt, if connected) => WorkSwitch analog instead of pin 4 (0V = lower end, 10/14V = upper end pos)
pin 6 (Fendt) => +Battery and via Stopp switch (5A max for ISO plug!)
pin 7 (Fendt) => -Battery

Company: https://github.com/gormr

# RS485 / ModbusRTU

# I2C external or WS2812 LED stripe


Sparkfunk part PRT-14417
SM04B-SRSS-TB(LF)(SN)
QWIIC SMD JST

e.g.: http://www.amazon.de/dp/B08JV9J36T/

P1: Weidmuller 1289550000 + 1372870000
S2C-SMT 3.50/24/90LF 3.2SN BK BX + B2CF 3.50/24/180LH SN BK BX

# ADC

# Wheel Angle Sensor


Use Teensy Ethernet picktail to connect to Bynav Ethernet for configuration

## LED colors: white: power


green/blue: serial data RxD/TxD
yellow/orange: I/O
red: error

USB A/F 90 Outside the buckle straight foot

Protected General Propose Inputs

# USB-C Power Delivery Role Swap


Switch Mode Power Supply 5V

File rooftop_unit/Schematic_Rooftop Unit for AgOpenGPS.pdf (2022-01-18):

+3V3

# Host Connector


Ardusimple Module(s) via Pixhawk connector

SM06B-GHS-TB(LF)(SN)

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

RichStratton (https://agopengps.discourse.group/t/dual-gps-setups/1067/231)

Info: X-connection has 2mm pitch

Two cables with 2 connectors JST GHR-06V-S, Crimp: SSHL-002T-P0.2

Option: RS232 for sprayer
e.g.: https://de.aliexpress.com/item/2054995985.html

Option: THT IMU Module / QWIIC

QWIIC
QWIIC SMD JST
SM04B-SRSS-TB(LF)(SN)

Company: agopengps.discourse.group

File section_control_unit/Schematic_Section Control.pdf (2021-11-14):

# USB-C PC/Tablet

## LED colors:


white: power
green/blue: serial data RxD/TxD
yellow/orange: I/O
red: error

USB: only needed if not connected to Central Unit

from Central Unit Board

DSR# 10 RI# 11 DCD# 12 DTR# 13 RTS# 14 TNOW 15 VCC 16 +5V

e. g. https://de.aliexpress.com/item/32843855386.html

https://www.arduino.cc/en/Tutorial/BuiltInExamples/ArduinoISP

Company:https://discourse.agopengps.com

# General options


auto-off-on switching @ SW1..8:
latching SPDT rocker switch on-off-on,
JP6 open
auto-off switching @ SW1..8:
latching SPST rocker switch on-off,
SW0 not mounted

Option for 48-PWM satellite

(temporary SPDT rocker switch (on)-off-(on))


# Switch Mode Power Supply Batt => 5V (needed for Ethernet and Wifi only)


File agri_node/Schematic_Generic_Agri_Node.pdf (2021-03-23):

# DS 10 D0 11 D1 12 D2 13 D3 14 CE# 15 VCC 16

24 Digital Inputs | 24 Digital Outputs


STCP and SHCP twisted in V1.0!!

Company: agopengps.discourse.group

# Option: RS485 / ModbusRTU / WS2811 Option: CAN2.0


Switch Mode Power Supply

# 16bit ADC



# Signals: Connect to plugs via 1kOhm

# or: Connect 12V to plugs via fuse


or: Connect 5V/0V to plugs with jumper 3.5mm industrial push⁻in connectors

# ESP32


Distance e. g.: https://de.aliexpress.com/item/4001287816907.html
RS232 e.g.: https://de.aliexpress.com/item/2054995985.html
Option: RS232/Distance

QWIIC SMD JST
SM04B-SRSS-TB(LF)(SN)
Sparkfunk part PRT-14417

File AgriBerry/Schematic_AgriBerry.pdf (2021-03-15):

# CAN1

# Raspberry Pi 4B


LED colors:
white: power
green/blue: serial data RxD/TxD
yellow/orange: I/O
red: error

Four protected digital or analog inputs

Two protected digital outputs

e.g.: https://de.aliexpress.com/item/2054995985.html

Company: agopengps.discourse.group

+5V

C7 +14V


Switch Mode Power Supply 5V 3A

Option to control a 6/2 valve

# Wheel Angle Sensor

+5V +5V


Ardusimple Module(s) via Pixhawk connector

GND 10 INT1 11 GND 12 NC 13 VDD 14 NC 15 NC 16 1K

QWIIC SMD JST
SM04B-SRSS-TB(LF)(SN)
Sparkfunk part PRT-14417

RichStratton (https://agopengps.discourse.group/t/dual-gps-setups/1067/231)

Info: X-connection has 2mm pitch

Two cables with 2 connectors JST GHR-06V-S, Crimp: SSHL-002T-P0.2

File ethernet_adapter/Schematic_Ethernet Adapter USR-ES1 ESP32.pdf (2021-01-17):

# Option: ESP32

+3V3


D2/Ch_A = Interrupt option (usually unused)

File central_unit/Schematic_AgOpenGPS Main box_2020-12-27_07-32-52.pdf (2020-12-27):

# Roof Top Unit Connector

+5V


USB-C PC/Tablet USB-C Charger/GP

DC/AUX KH-TYPE-C-16P
VBUS A9 SUB1 A8 DN1 A7 DP1 A6 CC1 A5 VBUS A4

LED colors:
white: power
green/blue: serial data RxD/TxD
yellow/orange: I/O
red: error

GND
2 USB Options for Modbus RTU, CAN, etc.

REXT 14 DMU 15 DPU 16 XRSTJ 17 VBUSM 18 BUSJ 19 VDD5 20 VD33_O 21 DRV 22 LED1 23 LED2 24 PWRJ 25 OVCJ 26 TESTJ 27 VD18 28

+5V

+5V


DSR# 10 RI# 11 DCD# 12 DTR# 13 RTS# 14 TNOW 15 VCC 16

Protected General Propose Inputs

# PIO0_28/SPIFI_IO2 44 VBAT 45

# CANtact


GND
DNP R83 for MSC
Populate for DFU
https://cantact.io/cantact-pro/users-guide.html

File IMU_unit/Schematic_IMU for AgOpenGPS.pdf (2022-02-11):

+3V3

+3V3


Sparkfunk part PRT-14417
SM04B-SRSS-TB(LF)(SN)
QWIIC SMD JST

Company:https://github.com/gormr

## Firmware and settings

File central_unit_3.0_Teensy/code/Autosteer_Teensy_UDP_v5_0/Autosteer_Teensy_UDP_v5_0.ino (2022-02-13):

/*
   UDP Autosteer code for Teensy 4.1
   For AgOpenGPS
   24 Nov 2021
   Like all Arduino code - copied from somewhere else :)
   So don't claim it as your own
*/

////////////////// User Settings /////////////////////////

//How many degrees before decreasing Max PWM
#define LOW_HIGH_DEGREES 5.0

/*  PWM Frequency ->
     490hz (default) = 0
     122hz = 1
     3921hz = 2
*/
#define PWM_Frequency 0

/////////////////////////////////////////////

// if USB power delivery is not available, comment out
//#define USB_PD

// if not in eeprom, overwrite
#define EEP_Ident 5100

// Address of CMPS14 shifted right one bit for arduino wire library
#define CMPS14_ADDRESS 0x60

// BNO08x definitions
#define REPORT_INTERVAL 90 //Report interval in ms (same as the delay at the bottom)

//   ***********  Motor drive connections  **************888
//Connect ground only for cytron, Connect Ground and +5v for IBT2

//Dir1 for Cytron Dir, Both L and R enable for IBT2
#define DIR1_RL_ENABLE  4

//PWM1 for Cytron PWM, Left PWM for IBT2
#define PWM1_LPWM  2

//Not Connected for Cytron, Right PWM for IBT2
#define PWM2_RPWM  3

//--------------------------- Switch Input Pins ------------------------
#define STEERSW_PIN 32
#define WORKSW_PIN 34
#define REMOTE_PIN 37


//Define sensor pin for current or pressure sensor
#define ANALOG_SENSOR_PIN A0

#define CONST_180_DIVIDED_BY_PI 57.2957795130823

#include <Wire.h>
extern TwoWire Wire1;

#include "tcpm_driver.h"  // **USB-PD**
#include "usb_pd.h"

const int usb_pd_int_pin = 35;
const int debug_led_pin  = 13;
const int debug0 = 11;
const int debug1 = 12;
const int enableDCDC = 36;

// USB-C Specific - TCPM start 1
const struct tcpc_config_t tcpc_config[CONFIG_USB_PD_PORT_COUNT] = {
  {0, fusb302_I2C_SLAVE_ADDR, &fusb302_tcpm_drv},
};
// USB-C Specific - TCPM end 1

#include <EEPROM.h>
#include "zADS1115.h"
ADS1115_lite adc(ADS1115_DEFAULT_ADDRESS);     // Use this for the 16-bit version ADS1115

#include <IPAddress.h>
#include "BNO08x_AOG.h"

// ethernet
#include <NativeEthernet.h>
#include <NativeEthernetUdp.h>

// ethernet interface ip address
// static uint8_t myip[] = { 192, 168, 1, 73 };
// TODO: Change the ipaddress? Or is it a replacement
IPAddress myip(192, 168, 0, 123);

// gateway ip address
static uint8_t gwip[] = { 192, 168, 0, 1 };

//DNS- you just need one anyway
static uint8_t myDNS[] = { 8, 8, 8, 8 };

//mask
static uint8_t mask[] = { 255, 255, 255, 0 };

//this is port of this autosteer module
uint16_t NTRIPUDPport = 2233;
uint16_t GNSSUDPport  = 5544;
uint16_t steerUDPport = 8888;
uint16_t AOGUDPport   = 9999;  //AOG port that listens

EthernetUDP udpNTRIP;
EthernetUDP udpSteer;

//sending back to where and which port
//static uint8_t ipDestination[] = {192, 168, 1, 255};
IPAddress ipDestination(192, 168, 0, 255);

// ethernet mac address - must be unique on your network
static uint8_t mymac[] = { 0x70, 0x69, 0x69, 0x2D, 0x30, 0x31 };

//uint8_t Ethernet::buffer[200]; // udp send and receive buffer
uint8_t udpData[UDP_TX_PACKET_MAX_SIZE];  // Buffer For Receiving UDP Data

// An EthernetUDP instance to let us send and receive packets over UDP
EthernetUDP Udp;

//loop time variables in microseconds
const uint16_t LOOP_TIME = 25;  //40Hz
uint32_t lastTime = LOOP_TIME;
uint32_t currentTime = LOOP_TIME;
uint32_t lastNMEATime = 0;

const uint16_t WATCHDOG_THRESHOLD = 100;
const uint16_t WATCHDOG_FORCE_VALUE = WATCHDOG_THRESHOLD + 2; // Should be greater than WATCHDOG_THRESHOLD
uint8_t watchdogTimer = WATCHDOG_FORCE_VALUE;

//show life in AgIO
uint8_t helloAgIO[] = {0x80, 0x81, 0x7f, 0xC7, 1, 0, 0x47 };
uint8_t helloCounter = 0;

//fromAutoSteerData FD 253 - ActualSteerAngle*100 -5,6, SwitchByte-7, pwmDisplay-8
uint8_t AOG[] = {0x80, 0x81, 0x7f, 0xFD, 8, 0, 0, 0, 0, 0, 0, 0, 0, 0xCC };
int16_t AOGSize = sizeof(AOG);

// F9P input data
const uint8_t NO_OF_NMEA_SENTENCES = 2;  // 2 sentences per time
const uint16_t NMEA_MAX_BYTES = 500;
uint8_t noOfF9Ps = 0;
uint8_t F9P_1[2*NMEA_MAX_BYTES];
uint8_t F9P_1state = 0;
uint16_t F9P_1cnt = 0;
uint8_t F9P_2[NMEA_MAX_BYTES];
uint16_t F9P_2cnt = 0;
uint8_t F9P_2state = 0;

// booleans to see if we are using CMPS or BNO08x
bool useCMPS = false;
bool useBNO08x = false;

// BNO08x address variables to check where it is
const uint8_t bno08xAddresses[] = {0x4A, 0x4B};
const int16_t nrBNO08xAdresses = sizeof(bno08xAddresses) / sizeof(bno08xAddresses[0]);
uint8_t bno08xAddress;
BNO080 bno08x;

float bno08xHeading = 0;
double bno08xRoll = 0;
double bno08xPitch = 0;

int16_t bno08xHeading10x = 0;
int16_t bno08xRoll10x = 0;

//EEPROM
int16_t EEread = 0;

//Relays
bool isRelayActiveHigh = true;
uint8_t relay = 0, relayHi = 0, uTurn = 0;
uint8_t tram = 0;

//Switches
uint8_t remoteSwitch = 0, workSwitch = 0, steerSwitch = 1, switchByte = 0;

//On Off
uint8_t guidanceStatus = 0;

//speed sent as *10
float gpsSpeed = 0;

//steering variables
float steerAngleActual = 0;
float steerAngleSetPoint = 0; //the desired angle from AgOpen
int16_t steeringPosition = 0; //from steering sensor
float steerAngleError = 0; //setpoint - actual

// Where is this for?
float CurrentSpeed = 0.0;

//pwm variables
int16_t pwmDrive = 0, pwmDisplay = 0;
float pValue = 0;
float errorAbs = 0;
float highLowPerDeg = 0;

//Steer switch button  ***********************************************************************************************************
uint8_t currentState = 1, reading, previous = 0;
uint8_t pulseCount = 0; // Steering Wheel Encoder
bool encEnable = false; //debounce flag
uint8_t thisEnc = 0, lastEnc = 0;

//Variables for settings
struct Storage {
  uint8_t Kp = 40;  //proportional gain
  uint8_t lowPWM = 10;  //band of no action
  int16_t wasOffset = 0;
  uint8_t minPWM = 9;
  uint8_t highPWM = 60;//max PWM value
  float steerSensorCounts = 30;
  float AckermanFix = 1;     //sent as percent
};  Storage steerSettings;  //11 bytes

//Variables for settings - 0 is false
struct Setup {
  uint8_t InvertWAS = 0;
  uint8_t IsRelayActiveHigh = 1; //if zero, active low (default)
  uint8_t MotorDriveDirection = 0;
  uint8_t SingleInputWAS = 1;
  uint8_t CytronDriver = 0;
  uint8_t SteerSwitch = 0;  //1 if switch selected
  uint8_t SteerButton = 0;  //1 if button selected
  uint8_t ShaftEncoder = 0;
  uint8_t PressureSensor = 0;
  uint8_t CurrentSensor = 0;
  uint8_t PulseCountMax = 5;
  uint8_t IsDanfoss = 0;
};  Setup steerConfig;          //9 bytes

//reset function
void(* resetFunc) (void) = 0;

int currentPos = 0;

unsigned char serial2buffer[128];
unsigned char serial7buffer[128];

void setup()
{
  Serial2.begin(460800);  // F9P_2
  Serial2.addMemoryForRead(serial2buffer, sizeof(serial2buffer));  
  Serial7.begin(460800);  // F9P_1
  Serial7.addMemoryForRead(serial7buffer, sizeof(serial7buffer));  
  Serial.begin(38400);
  delay(100);
  Serial.println("Setup");
  //PWM rate settings. Set them both the same!!!!
  /*  PWM Frequency ->
       490hz (default) = 0
       122hz = 1
       3921hz = 2
  */
  if (PWM_Frequency == 0)
  {
    analogWriteFrequency(PWM1_LPWM, 490);
    analogWriteFrequency(PWM2_RPWM, 490);
  }
  else if (PWM_Frequency == 1)
  {
    analogWriteFrequency(PWM1_LPWM, 122);
    analogWriteFrequency(PWM2_RPWM, 122);
  }
  else if (PWM_Frequency == 2)
  {
    analogWriteFrequency(PWM1_LPWM, 3921);
    analogWriteFrequency(PWM2_RPWM, 3921);
  }

  //keep pulled high and drag low to activate, noise free safe
  pinMode(WORKSW_PIN, INPUT_PULLUP);
  pinMode(STEERSW_PIN, INPUT_PULLUP);
  pinMode(REMOTE_PIN, INPUT_PULLUP);
  pinMode(DIR1_RL_ENABLE, OUTPUT);

  pinMode(debug0, OUTPUT);
  pinMode(debug1, OUTPUT);
  pinMode(enableDCDC, OUTPUT);
  digitalWrite(enableDCDC, LOW);

#ifdef USB_PD
  pinMode(usb_pd_int_pin, INPUT_PULLUP);   // **USB-PD**
  pinMode(debug_led_pin, OUTPUT);
  digitalWrite(debug_led_pin, LOW);
#endif

  if (steerConfig.CytronDriver) pinMode(PWM2_RPWM, OUTPUT);

  //set up communication
  //Wire.begin();
  Wire1.begin();

   //test if CMPS working
  uint8_t error;
  Wire1.beginTransmission(CMPS14_ADDRESS);
  error = Wire1.endTransmission();

  if (error == 0)
  {
    Serial.println("Error = 0");
    Serial.print("CMPS14 ADDRESs: 0x");
    Serial.println(CMPS14_ADDRESS, HEX);
    Serial.println("CMPS14 Ok.");
    useCMPS = true;
  }
  else
  {
    Serial.println("Error = 4");
    Serial.println("CMPS not Connected or Found");
    useCMPS = false;
  }

  // Check for BNO08x
  if (!useCMPS)
  {
    for (int16_t i = 0; i < nrBNO08xAdresses; i++)
    {
      bno08xAddress = bno08xAddresses[i];

      Serial.print("\r\nChecking for BNO08X on ");
      Serial.println(bno08xAddress, HEX);
      Wire1.beginTransmission(bno08xAddress);
      error = Wire1.endTransmission();

      if (error == 0)
      {
        Serial.println("Error = 0");
        Serial.print("BNO08X ADDRESs: 0x");
        Serial.println(bno08xAddress, HEX);
        Serial.println("BNO08X Ok.");

        // Initialize BNO080 lib
        if (bno08x.begin(bno08xAddress, Wire1))
        {
          Wire1.setClock(400000); //Increase I2C data rate to 400kHz

          // Use gameRotationVector
          bno08x.enableGameRotationVector(REPORT_INTERVAL); //Send data update every REPORT_INTERVAL in ms for BNO085

          // Retrieve the getFeatureResponse report to check if Rotation vector report is corectly enable
          if (bno08x.getFeatureResponseAvailable() == true)
          {
            if (bno08x.checkReportEnable(SENSOR_REPORTID_GAME_ROTATION_VECTOR, REPORT_INTERVAL) == false) bno08x.printGetFeatureResponse();

            // Break out of loop
            useBNO08x = true;
            break;
          }
          else
          {
            Serial.println("BNO08x init fails!!");
          }
        }
        else
        {
          Serial.println("BNO080 not detected at given I2C address.");
        }
      }
      else
      {
        Serial.println("Error = 4");
        Serial.println("BNO08X not Connected or Found");
      }
    }
  }

  //50Khz I2C
  TWBR = 144;

  EEPROM.get(0, EEread);              // read identifier

  if (EEread != EEP_Ident)   // check on first start and write EEPROM
  {
    EEPROM.put(0, EEP_Ident);
    EEPROM.put(10, steerSettings);
    EEPROM.put(40, steerConfig);
  }
  else
  {
    EEPROM.get(10, steerSettings);     // read the Settings
    EEPROM.get(40, steerConfig);
  }

  // for PWM High to Low interpolator
  highLowPerDeg = ((float)(steerSettings.highPWM - steerSettings.lowPWM)) / LOW_HIGH_DEGREES;

  // start the Ethernet connection and the server:
  Ethernet.begin(mymac, myip);

  // Check for Ethernet hardware present
  if (Ethernet.hardwareStatus() == EthernetNoHardware) {
    Serial.println("Ethernet shield was not found.  Sorry, can't run without hardware. :(");
    while (true) {
      delay(1); // do nothing, no point running without Ethernet hardware
    }
  }
  if (Ethernet.linkStatus() == LinkOFF) {
    Serial.println("Ethernet cable is not connected.");
  }

  // start UDP
  udpSteer.begin(steerUDPport);
  udpNTRIP.begin(NTRIPUDPport);

  Serial.println("Setup complete, waiting for AgOpenGPS");

  adc.setSampleRate(ADS1115_REG_CONFIG_DR_128SPS); //128 samples per second
  adc.setGain(ADS1115_REG_CONFIG_PGA_6_144V);


#ifdef USB_PD
  tcpm_init(0);  // **USB-PD**
  delay(50);
  pd_init(0);
  delay(50);
#endif

}// End of Setup

void loop()
{
  int currentRoll = 0;
  int rollLeft = 0;
  int steerLeft = 0;
  
#ifdef USB_PD
  if (LOW == digitalRead(usb_pd_int_pin)) {       // **USB-PD**
      Serial.println("-------------------------int--------------------------------");
      tcpc_alert(0);
      Serial.println("------------------------endint------------------------------");
  }
  pd_run_state_machine(0);
#endif

  ReceiveUdp();

  // Loop triggers every 100 msec and sends back gyro heading, and roll, steer angle etc
  currentTime = millis();

  // NMEA received????
  if (Serial2.available() || Serial7.available())
  {
    if (currentTime > (lastNMEATime + 60))
    {
        //----------------------------------------------------------------------------
        //Serial Send to agopenGPS

        int16_t sa = (int16_t)(steerAngleActual * 100);

 
        AOG[5] = (uint8_t)sa;
        AOG[6] = sa >> 8;

        if (useCMPS)
        {
          Wire1.beginTransmission(CMPS14_ADDRESS);
          Wire1.write(0x02);
          Wire1.endTransmission();

          Wire1.requestFrom(CMPS14_ADDRESS, 2);
          while (Wire1.available() < 2);

          //the heading x10
          AOG[8] = Wire1.read();
          AOG[7] = Wire1.read();

          Wire1.beginTransmission(CMPS14_ADDRESS);
          Wire1.write(0x1C);
          Wire1.endTransmission();

          Wire1.requestFrom(CMPS14_ADDRESS, 2);
          while (Wire1.available() < 2);

          //the roll x10
          AOG[10] = Wire1.read();
          AOG[9] = Wire1.read();
        }
        else if (useBNO08x)
        {
          if (bno08x.dataAvailable() == true)
          {
            bno08xHeading = (bno08x.getYaw()) * CONST_180_DIVIDED_BY_PI; // Convert yaw / heading to degrees
            bno08xHeading = -bno08xHeading; //BNO085 counter clockwise data to clockwise data

            if (bno08xHeading < 0 && bno08xHeading >= -180) //Scale BNO085 yaw from [-180°;180°] to [0;360°]
            {
              bno08xHeading = bno08xHeading + 360;
            }

            bno08xRoll = (bno08x.getRoll()) * CONST_180_DIVIDED_BY_PI; //Convert roll to degrees
            //bno08xPitch = (bno08x.getPitch())* CONST_180_DIVIDED_BY_PI; // Convert pitch to degrees

            bno08xHeading10x = (int16_t)(bno08xHeading * 10);
            bno08xRoll10x = (int16_t)(bno08xRoll * 10);

            //Serial.print(bno08xHeading10x);
            //Serial.print(",");
            //Serial.println(bno08xRoll10x);

            //the heading x10
            AOG[7] = (uint8_t)bno08xHeading10x;
            AOG[8] = bno08xHeading10x >> 8;


            //the roll x10
            AOG[9] = (uint8_t)bno08xRoll10x;
            AOG[10] = bno08xRoll10x >> 8;
          }
        }
        else
        {
          //heading
          AOG[7] = (uint8_t)9999;
          AOG[8] = 9999 >> 8;

          //roll
          AOG[9] = (uint8_t)8888;
          AOG[10] = 8888 >> 8;

          if (rollLeft) 
            currentRoll = currentRoll - 10;
          else 
            currentRoll = currentRoll + 10;

          if (abs(currentRoll) > 20)
          {
            if(rollLeft)
            {
              rollLeft = 0;
            }
            else
            {
              rollLeft = 1;
            }
          }
          
          //roll
          AOG[9] = (uint8_t)currentRoll;
          AOG[10] = currentRoll >> 8;
        }

        AOG[11] = switchByte;
        AOG[12] = (uint8_t)pwmDisplay;

        //checksum
        int16_t CK_A = 0;
        for (uint8_t i = 2; i < AOGSize - 1; i++)
          CK_A = (CK_A + AOG[i]);

        AOG[AOGSize - 1] = CK_A;

        //off to AOG
        SendUdp(AOG, sizeof(AOG), ipDestination, AOGUDPport);

        // Stop sending the helloAgIO message
        helloCounter = 0;

        F9P_1state = 0;
        F9P_2state = 0;
        F9P_1cnt = 0;
        F9P_2cnt = 0;
    }
    
    while (Serial7.available()) 
    {
      if (F9P_1cnt < NMEA_MAX_BYTES)
      {
        F9P_1[F9P_1cnt] = Serial7.read();
        if ((F9P_1cnt & 0xfff0) && F9P_1[F9P_1cnt] == 0x0a && F9P_1[F9P_1cnt - 1] == 0x0d)  F9P_1state++;    // <CR><LF>" detected in NMEA string => got full sentence
        if (F9P_1state == NO_OF_NMEA_SENTENCES)  noOfF9Ps |= 1;  // detect F9P as valid when correct no of sentences is received once
        F9P_1cnt++;
      } 
      else 
      {
        Serial7.read();
        F9P_1cnt = 0;
        F9P_1state = 0;
      }
    }

    while (Serial2.available())
    {
      if (F9P_2cnt < NMEA_MAX_BYTES)
      {
        F9P_2[F9P_2cnt] = Serial2.read();
        if ((F9P_2cnt & 0xfff0) && F9P_2[F9P_2cnt] == 0x0a && F9P_2[F9P_2cnt - 1] == 0x0d)  F9P_2state++;    // <CR><LF>" detected in NMEA string => got full sentence
        if (F9P_2state == NO_OF_NMEA_SENTENCES)  noOfF9Ps |= 2;
        F9P_2cnt++;
      } 
      else 
      {
        Serial2.read();
        F9P_2cnt = 0;
        F9P_2state = 0;
      }
    }

    if ((noOfF9Ps == 3 && F9P_1state == NO_OF_NMEA_SENTENCES && F9P_2state == NO_OF_NMEA_SENTENCES) || 
        (noOfF9Ps == 1 && F9P_1state == NO_OF_NMEA_SENTENCES) || 
        (noOfF9Ps == 2 && F9P_2state == NO_OF_NMEA_SENTENCES))
    {
//      digitalWrite(debug0, HIGH);
      uint16_t i;
      for (i = F9P_1cnt; i < (F9P_1cnt + F9P_2cnt); i++) 
          F9P_1[i] = F9P_2[i-F9P_1cnt];  // concat strings
      SendUdp(F9P_1, i, ipDestination, GNSSUDPport);
  
      Serial.print("\"");
      for (uint16_t j=0; j<i; j++) Serial.write(F9P_1[j]);  // debug
      Serial.print("\" Units: ");
      Serial.println(noOfF9Ps);
//      digitalWrite(debug0, LOW);
      F9P_1cnt = 0;
      F9P_1state = 0;
      F9P_2cnt = 0;
      F9P_2state = 0;
    }
   
    lastNMEATime = currentTime;
  }
  

  if (currentTime - lastTime >= LOOP_TIME)
  {
    lastTime = currentTime;

    //reset debounce
    encEnable = true;

    //If connection lost to AgOpenGPS, the watchdog will count up and turn off steering
    if (watchdogTimer++ > 250) watchdogTimer = WATCHDOG_FORCE_VALUE;

    //read all the switches
    workSwitch = digitalRead(WORKSW_PIN);  // read work switch

    if (steerConfig.SteerSwitch == 1)         //steer switch on - off
    {
      steerSwitch = digitalRead(STEERSW_PIN); //read auto steer enable switch open = 0n closed = Off
    }
    else if (steerConfig.SteerButton == 1)    //steer Button momentary
    {
      reading = digitalRead(STEERSW_PIN);
      if (reading == LOW && previous == HIGH)
      {
        if (currentState == 1)
        {
          currentState = 0;
          steerSwitch = 0;
        }
        else
        {
          currentState = 1;
          steerSwitch = 1;
        }
      }
      previous = reading;
    }
    else                                      // No steer switch and no steer button
    {
      // So set the correct value. When guidanceStatus = 1,
      // it should be on because the button is pressed in the GUI
      // But the guidancestatus should have set it off first
      if (guidanceStatus == 1 && steerSwitch == 1 && previous == 0)
      {
        steerSwitch = 0;
        previous = 1;
      }

      // This will set steerswitch off and make the above check wait until the guidanceStatus has gone to 0
      if (guidanceStatus == 0 && steerSwitch == 0 && previous == 1)
      {
        steerSwitch = 1;
        previous = 0;
      }
    }

    if (steerConfig.ShaftEncoder && pulseCount >= steerConfig.PulseCountMax)
    {
      steerSwitch = 1; // reset values like it turned off
      currentState = 1;
      previous = 0;
    }

    // Current sensor?
    if (steerConfig.CurrentSensor)
    {
      int16_t analogValue = analogRead(ANALOG_SENSOR_PIN);

      // When the current sensor is reading current high enough, shut off
      if (abs(((analogValue - 512)) / 10.24) >= steerConfig.PulseCountMax) //amp current limit switch off
      {
        steerSwitch = 1; // reset values like it turned off
        currentState = 1;
        previous = 0;
      }
    }

    // Pressure sensor?
    if (steerConfig.PressureSensor)
    {
      int16_t analogValue = analogRead(ANALOG_SENSOR_PIN);

      // Calculations below do some assumptions, but we should be close?
      // 0-250bar sensor 4-20ma with 150ohm 1V - 5V -> 62,5 bar/V
      // 5v  / 1024 values -> 0,0048828125 V/bit
      // 62,5 * 0,0048828125 = 0,30517578125 bar/count
      // 1v = 0 bar = 204,8 counts
      int16_t steeringWheelPressureReading = (analogValue - 204) * 0.30517578125;

      // When the pressure sensor is reading pressure high enough, shut off
      if (steeringWheelPressureReading >= steerConfig.PulseCountMax)
      {
        steerSwitch = 1; // reset values like it turned off
        currentState = 1;
        previous = 0;
      }
    }

    remoteSwitch = digitalRead(REMOTE_PIN); //read auto steer enable switch open = 0n closed = Off
    switchByte = 0;
    switchByte |= (remoteSwitch << 2); //put remote in bit 2
    switchByte |= (steerSwitch << 1);   //put steerswitch status in bit 1 position
    switchByte |= workSwitch;

    /*
      #if Relay_Type == 1
        SetRelays();       //turn on off section relays
      #elif Relay_Type == 2
        SetuTurnRelays();  //turn on off uTurn relays
      #endif
    */

    //get steering position
    if (steerConfig.SingleInputWAS)   //Single Input ADS
    {
      adc.setMux(ADS1115_REG_CONFIG_MUX_SINGLE_0);
      steeringPosition = adc.getConversion();
      adc.triggerConversion();//ADS1115 Single Mode

      steeringPosition = (steeringPosition >> 1); //bit shift by 2  0 to 13610 is 0 to 5v
    }
    else    //ADS1115 Differential Mode
    {
      adc.setMux(ADS1115_REG_CONFIG_MUX_DIFF_0_1);
      steeringPosition = adc.getConversion();
      adc.triggerConversion();

      steeringPosition = (steeringPosition >> 1); //bit shift by 2  0 to 13610 is 0 to 5v
    }

    //DETERMINE ACTUAL STEERING POSITION

    //convert position to steer angle. 32 counts per degree of steer pot position in my case
    //  ***** make sure that negative steer angle makes a left turn and positive value is a right turn *****
    if (steerConfig.InvertWAS)
    {
      steeringPosition = (steeringPosition - 6805  - steerSettings.wasOffset);   // 1/2 of full scale
      steerAngleActual = (float)(steeringPosition) / -steerSettings.steerSensorCounts;
    }
    else
    {
      steeringPosition = (steeringPosition - 6805  + steerSettings.wasOffset);   // 1/2 of full scale
      steerAngleActual = (float)(steeringPosition) / steerSettings.steerSensorCounts;
    }

    //Ackerman fix
    if (steerAngleActual < 0) steerAngleActual = (steerAngleActual * steerSettings.AckermanFix);
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

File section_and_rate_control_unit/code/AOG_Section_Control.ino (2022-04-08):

/*
  Test code for SC board for AgOpenGPS

  Reads an analog input pin, maps the result to a range from 0 to 255 and uses
  the result to set the pulse width modulation (PWM) of an output pin.
  Also prints the results to the Serial Monitor.

  The circuit:
  - potentiometer connected to analog pin 7.
    Center pin of the potentiometer goes to the analog pin.
    side pins of the potentiometer go to +5V and ground
  - LED connected from digital pin 9 to ground through 220 ohm resistor

  created 29 Dec. 2021
  by GR

  This example code is in the public domain.
*/

/////////////////////////////////////////////////////////////////////////////////////////////////
// board options:
#define SPEEDINPUT 1  // define as 1, if section 0 shall be used as speed input (0 for section)
const uint8_t NUMBER_OF_SECTIONS = 7;   // mount the switches and relays RIGHT alligned!
/////////////////////////////////////////////////////////////////////////////////////////////////


#include <EEPROM.h>
#include <AceTMI.h>
#include <AceTMI.h> // SimpleTmiInterface
#include <AceSegment.h> // Tm1637Module

#define EEP_Ident 0x5005

//Program counter reset
void(* resetFunc) (void) = 0;

// display module:
using ace_tmi::SimpleTmi1637Interface;
using ace_segment::LedModule;
using ace_segment::Tm1637Module;
const uint8_t CLK_PIN = A5;
const uint8_t DIO_PIN = A4;
const uint8_t NUM_DIGITS = 4;

// Many TM1637 LED modules contain 10 nF capacitors on their DIO and CLK lines
// which are unreasonably high. This forces a 100 microsecond delay between
// bit transitions. If you remove those capacitors, you can set this as low as
// 1-5 micros.
const uint8_t DELAY_MICROS = 100;

using TmiInterface = SimpleTmi1637Interface;
TmiInterface tmiInterface(DIO_PIN, CLK_PIN, DELAY_MICROS);
Tm1637Module<TmiInterface, NUM_DIGITS> ledModule(tmiInterface);

// LED segment patterns.
const uint8_t NUM_PATTERNS = 10;
const uint8_t PATTERNS[NUM_PATTERNS] = {
  0b00111111, // 0
  0b00000110, // 1
  0b01011011, // 2
  0b01001111, // 3
  0b01100110, // 4
  0b01101101, // 5
  0b01111101, // 6
  0b00000111, // 7
  0b01111111, // 8
  0b01101111, // 9
};

//Variables for config - 0 is false
struct Config 
{
  uint8_t raiseTime = 2;
  uint8_t lowerTime = 4;
  uint8_t enableToolLift = 1;
  uint8_t isRelayActiveHigh = 1; // must always be 1 for section control board

};  Config aogConfig;   //4 bytes

const uint8_t LOOP_TIME = 20; //50hz
uint32_t lastTime = LOOP_TIME;
uint32_t currentTime = LOOP_TIME;
uint32_t fifthTime = 0;
uint16_t count = 0;
uint8_t recvState = 0;

//Comm checks
uint8_t watchdogTimer = 0;     //make sure we are talking to AOG
uint8_t serialResetTimer = 0;  //if serial buffer is getting full, empty it
uint8_t statusMainSwitch = 0;  // 0x80 and higher = on; also packet counter

// These constants won't change. They're used to give names to the pins used:
const int pressureInPin = A7;  // Analog input pin that the pressure sensor or potentiometer is attached to
const int flowInPin = A1;      // Digital input pin that the flow sensor or a pushbutton is attached to (can be used for another analog sensor as well)
const int speedInPin = 2;      // Digital input pin that the speed sensor or a pushbutton is attached to (option; 7 sections only in that case)
const int mainInPin = A6;      // Analog input pin for main switch (finally a digital input only)

const int secOutPin[] = {2, 3, 4, 5, 6, 7, 8, 9};      // Digital output for section x (0: instead of speed sensor)

const int pressureOutPin = A2; // Digital output for pressure modification (tristated if no mod)
const int levelOutPin = A3;    // Digital output for hydraulic rise/lower (tristated if no mod)

const int speedOutPin = 10;    // Digital output for speed PWM (from AgOpenGPS)

//The variables used for storage
uint8_t relayHi=0, relayLo = 0, gpsSpeed = 0, tramline = 0, tree = 0, uTurn = 0, hydLift = 0; 
uint8_t forceOffHi=0, forceOffLo = 0, forceOnHi = 0, forceOnLo = 0; 
uint8_t relayBack = 0;         // real relay status read from toggle switches
uint8_t raiseTimer = 0, lowerTimer = 0, lastTrigger = 0; 
bool isRaise = false;
bool isLower = false;

//Communication with AgOpenGPS
int16_t temp, EEread = 0;

//Parsing PGN
bool isPGNFound = false, isHeaderFound = false;
uint8_t pgn = 0, dataLength = 0, idx = 0;
int16_t tempHeader = 0;

uint8_t AOG[] = {0x80,0x81, 0x7b, 0xea, 8, 1, 0, 0, 0, 0,0,0,0, 0xCC };
// [5]: Bits: AOG section control AUTO, Section control OFF, Rate L+R ...
// [9]: relays low byte (0 on auto)
//[10]: 1 = forced off low byte
//[11]: relays high byte (0 on auto)
//[12]: 1 = forced off high byte
//
uint8_t Disp[] = {0, 0, 0, 0};   // LED display

int pressureValue = 0;         // value read from the pot or sensor
uint8_t flowValue = 0;         // value read from the flow sensor (simple counter for test)
uint8_t speedValue = 0;        // value read from the speed sensor (simple counter for test)

void setup()
{
  //set the baud rate
  Serial.begin(38400);
  while (!Serial) { ; } // wait for serial port to connect. Needed for native USB

  EEPROM.get(0, EEread);              // read identifier

  if (EEread != EEP_Ident)   // check on first start and write EEPROM
  {
    EEPROM.put(0, EEP_Ident);
    EEPROM.put(6, aogConfig);
  }
  else
  {
    EEPROM.get(6, aogConfig);
  }

  //set the pins for sections to be outputs (pin numbers)
  for (uint8_t i=0; i<9; i++)  pinMode(secOutPin[i], OUTPUT);  

  tmiInterface.begin();
  ledModule.begin();

  ledModule.setPatternAt(0, 0b00110001);
  ledModule.setPatternAt(1, 0b01111001);
  ledModule.setPatternAt(2, PATTERNS[5]);
  ledModule.setPatternAt(3, 0b00110001);

  ledModule.setBrightness(255);

  ledModule.flush();
}
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

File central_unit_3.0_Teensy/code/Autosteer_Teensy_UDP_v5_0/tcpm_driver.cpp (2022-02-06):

/*
 * tcpm_driver.c  // Type C Port Manager
 *
 * Created: 11/11/2017 18:42:26
 *  Author: jason
 */ 

#include "tcpm_driver.h"
#include "Arduino.h"
#include <Wire.h>

extern const struct tcpc_config_t tcpc_config[CONFIG_USB_PD_PORT_COUNT];

extern "C" {
  //#include <Wire.h>
const int debug0 = 11;
const int debug1 = 12;

  void WirebeginTransmission(int addr)
  {
    Wire1.beginTransmission(addr);
  }

  void Wirewrite(int value)
  {
    Wire1.write(value);
  }
  
  void WireendTransmission(int stopBit)
  {
    Wire1.endTransmission(stopBit);
  }

  void WirerequestFrom(int addr, int quantity, int stopBit)
  {
    Wire1.requestFrom(addr, quantity, stopBit);
  }

  int Wireread()
  {
    return Wire1.read();
  }
}

/* I2C wrapper functions - get I2C port / slave addr from config struct. */
int tcpc_write(int port, int reg, int val)
{
  digitalWrite(debug0, HIGH);
  WirebeginTransmission(fusb302_I2C_SLAVE_ADDR);
  Wirewrite(reg & 0xFF);
  Wirewrite(val & 0xFF);
  WireendTransmission(true);
  digitalWrite(debug0, LOW);
  
  Serial.print("[0x");
  Serial.print(reg < 16 ? "0" : "");
  Serial.print(reg, HEX);
  Serial.print("]=0x");  
  Serial.print(val < 16 ? "0" : "");
  Serial.println(val, HEX);

  return 0;
}

int tcpc_write16(int port, int reg, int val)
{
  WirebeginTransmission(fusb302_I2C_SLAVE_ADDR);
  Wirewrite(reg & 0xFF);
  Wirewrite(val & 0xFF);
  Wirewrite((val >> 8) & 0xFF);
  WireendTransmission(true);

  Serial.print("w16: ");
  Serial.print(reg);
  Serial.print(" := ");
  Serial.println(val);
  
  return 0;
}

int tcpc_read(int port, int reg, int *val)
{
  digitalWrite(debug1, HIGH);
  WirebeginTransmission(fusb302_I2C_SLAVE_ADDR);
  Wirewrite(reg & 0xFF);
  WireendTransmission(false);
  WirerequestFrom(fusb302_I2C_SLAVE_ADDR, 1, true);
  *val = Wireread();
  digitalWrite(debug1, LOW);

  Serial.print("          [0x");
  Serial.print(reg < 16 ? "0" : "");
  Serial.print(reg, HEX);
  Serial.print("]: 0x");  
  Serial.print(*val < 16 ? "0" : "");
  Serial.println(*val, HEX);

  return 0;
}

int tcpc_read16(int port, int reg, int *val)
{
  WirebeginTransmission(fusb302_I2C_SLAVE_ADDR);
  Wirewrite(reg & 0xFF);
  WireendTransmission(false);
  WirerequestFrom(fusb302_I2C_SLAVE_ADDR, 1, true);
  *val  = Wireread();
  *val |= (Wireread() << 8);

  Serial.print("r16: ");
  Serial.print(reg);
  Serial.print(": ");
  Serial.println(*val);

  return 0;
}

int tcpc_xfer(int port,
	const uint8_t *out, int out_size,
	uint8_t *in, int in_size,
	int flags)
{
  if (out_size)
  {
    WirebeginTransmission(fusb302_I2C_SLAVE_ADDR);
    for (; out_size>0; out_size--) {
      Wirewrite(*out);
      out++;
    }
    if (flags & I2C_XFER_STOP)
    {
      WireendTransmission(true);
    }
    else
    {
      WireendTransmission(false);
    }
  }

  if (in_size) {
    WirerequestFrom(fusb302_I2C_SLAVE_ADDR, in_size, (flags & I2C_XFER_STOP));
    for (; in_size>0; in_size--) {
        *in = Wireread();
        in++;
    }
  }

  return 0;
}

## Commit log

2020-12-27 ESP32: connections corrected
    [BOM_AgOpenGPS_ASU_2020-12-25_22-28-50.csv, PickAndPlace_PCB_AgOpenGPS_ASU_2020-12-27_17-45-33.csv]
2020-12-28 overview picture
    [BOM_PCB_AgOpenGPS_RTU_2020-12-27_17-49-28.csv, ESP32 ublox IMU_2020-12-27_17-32-34.schdoc, PCB_AgOpenGPS_RTU_2020-12-27_17-55-25.pcbdoc]
2020-12-28 qwiic connector added
    [BOM_PCB_AgOpenGPS_RTU_2020-12-27_17-49-28.csv, ESP32 ublox IMU_2020-12-27_17-32-34.schdoc, PCB_AgOpenGPS_RTU_2020-12-27_17-55-25.pcbdoc]
2020-12-31 qwiic, SPI, RS232, CMPS14, Pixhawk added
    [BOM_PCB_AgOpenGPS_RTU_2020-12-27_17-49-28.csv, ESP32 ublox IMU_2020-12-27_17-32-34.schdoc, PCB_AgOpenGPS_RTU_2020-12-27_17-55-25.pcbdoc]
2021-01-03 main update
    [BOM_AgOpenGPS_ASU_2020-12-25_22-28-50.csv, BOM_Central Unit for AgOpenGPS.csv, BOM_PCB_AgOpenGPS_RTU_2020-12-27_17-49-28.csv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]
2021-01-03 pinning updated to https://github.com/Jeep1945/Dualheading
    [Rooftop Unit for AgOpenGPS.schdoc, Rooftop_Unit_AgOpenGPS.pcbdoc]
2021-01-04 CMPS14 and holes for Ardusimple added
    [PickAndPlace_Central_Unit_AgOpenGPS.csv]
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2021-01-06 bugfix GNSS module placement
    [ESP32 ublox IMU.schdoc, PickAndPlace_Central_Unit_AgOpenGPS.csv, Rooftop_Unit_AgOpenGPS.pcbdoc]
2021-01-08 parts adapted to JLCPCB
    [BOM_Central Unit for AgOpenGPS.csv, BOM_THT_Central Unit for AgOpenGPS.csv, Central_Unit_AgOpenGPS.pcbdoc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]
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2021-01-15 bugfix MEMS footprint
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2021-01-17 12V supply option added
    [ESP32 ublox IMU.schdoc, Rooftop_Unit_AgOpenGPS.pcbdoc]
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2021-01-21 footprint and value update 8.2kOhm
    [BOM_Central Unit for AgOpenGPS.csv]
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2021-01-22 bugfix LED designators
    [BOM_Central Unit for AgOpenGPS.csv, PickAndPlace_Central_Unit_AgOpenGPS.csv]
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2021-02-09 6/2 valve option added
    [BOM_Central Unit for AgOpenGPS.csv, BOM_JLCPCB_not_available.csv, JLCPCB_not_available.csv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]
2021-02-12 BOM for Shenzhen2u added
    [BOM_Central Unit for AgOpenGPS__JLCPCB.csv, BOM_Central Unit for AgOpenGPS__Shenzhen2u .xlsx]
2021-02-12 2nd sources updated to BOM
    [BOM_Central Unit for AgOpenGPS.csv, BOM_Central Unit for AgOpenGPS__JLCPCB.csv]
2021-02-14 bugfix THT BOM
    [BOM_THT_Central Unit for AgOpenGPS.csv]
2021-02-14 links added to THT BOM
    [BOM_THT_Central Unit for AgOpenGPS.csv]
2021-02-14 links added to BOM of missing parts
    [BOM_JLCPCB_not_available.csv]
2021-02-15 minor bugfix BOM: WAS2, WAS3
    [BOM_Central Unit for AgOpenGPS__JLCPCB.csv, BOM_Central Unit for AgOpenGPS__Shenzhen2u .xlsx]
2021-02-16 minor bug fix: rotation of Q8
    [PickAndPlace_Central_Unit_AgOpenGPS.csv]
2021-02-17 minor bug fix: R11, R12, R24 slightly shifted
    [PickAndPlace_Central_Unit_AgOpenGPS.csv]
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2021-02-18 BOM + PnP reworked
    [BOM_Central Unit for AgOpenGPS__JLCPCB.csv, Infomation_only_Lib_parts_with_wrong_rotation.csv, PickAndPlace_Central_Unit_AgOpenGPS.csv]
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2021-02-20 M8/M12 sources for US/worldwide added
    [BOM_THT_Central Unit for AgOpenGPS.csv]
2021-02-20 R97 = n. m.
    [BOM_Central Unit for AgOpenGPS__JLCPCB.csv, BOM_Central Unit for AgOpenGPS__Shenzhen2u .xlsx]
2021-02-21 V1.6 bugfix USB-C R43, R46, Q7
    [BOM_Central Unit for AgOpenGPS__JLCPCB.csv, PickAndPlace_Central_Unit_AgOpenGPS.csv]
2021-02-28 V1.7 PCB size adapted to housing
    [PickAndPlace_Central_Unit_AgOpenGPS.csv]
2021-02-28 DXF milling files added
    [milling_left_side.DXF, milling_right_side.DXF]
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2021-03-16 BOM update to basic parts
    [BOM_AgriBerry.csv, BOM_Minimal_AgriBerry.csv, PickAndPlace_AgriBerry.csv]
2021-03-17 minor: PnP correction
    [PickAndPlace_AgriBerry.csv]
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2021-03-21 Q8, Q9 added; code for Atmel added
    [BOM_Central Unit for AgOpenGPS__JLCPCB.csv, PickAndPlace_Central_Unit_AgOpenGPS.csv]
2021-03-29 V1.8: ESP32 adapted to mtz8302/AOG_Autosteer_ESP32
    [BOM_Central Unit for AgOpenGPS__JLCPCB.csv, PickAndPlace_Central_Unit_AgOpenGPS.csv]
2021-03-29 1mm shortend
    [PickAndPlace_AgriBerry.csv]
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2021-04-18 V1.9 - see changelog!
    [BOM_Central Unit for AgOpenGPS__JLCPCB.csv, BOM_Central Unit for AgOpenGPS__JLCPCB_SMD_only.csv, BOM_Central Unit for AgOpenGPS__Shenzhen2u .xlsx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]
2021-11-14 New: Section control and Control Unit 2.0
    [BOM_CentralUnit2.0.csv, BOM_SectionControlUnit.csv, PickAndPlace_CentralUnit2.0.csv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]
2021-11-14 new structure: V2.0=Brian, V3.0=Teensy
    [BOM_CentralUnit2.0.csv, BOM_CentralUnit3.0.csv, PickAndPlace_CentralUnit2.0.csv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]
2021-12-12 BOM adapted to JLCPCB
    BOM adapted to JLCPCB
    [BOM_CentralUnit2.0.csv, BOM_CentralUnit2.0_modified.csv, BOM_CentralUnit3.0.csv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]
2021-12-12 BOM optimized for JLCPCB
    [BOM_SectionControlUnit.csv, BOM_SectionControlUnit_modified.csv]
2021-12-13 update, becauses JLC detected an error inside Gerber
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2021-12-31 discharge resistors added for read-back
    [BOM_SectionControlUnit.csv, BOM_SectionControlUnit_modified.csv, PickAndPlace_SectionControlUnit.csv]
2022-01-01 mechanical drawing for front panel added on mechanic layer
    [Frontpanel_SectionControlUnit_7Sec.dxf]
2022-01-01 reduced to one layer
    [Frontpanel_SectionControlUnit_7Sec.dxf]
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2022-01-05 CAD update side plate
    [left_side.dxf, right_side.dxf]
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2022-01-06 - R64 connected to 3V3 instead of 5V - D31 removed, jumper USB_SC added
    [BOM_CentralUnit2.0_modified.csv, PickAndPlace_CentralUnit2.0.csv]
2022-01-07 some bugfixes
    [BOM_CentralUnit2.0_modified.csv, PickAndPlace_CentralUnit2.0.csv]
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2022-01-09 mod for 24V motors
    [BOM_CentralUnit2.0_modified.csv, BOM_CentralUnit3.0_modified.csv, PickAndPlace_CentralUnit2.0.csv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]
2022-01-10 W5500 bugfix
    [BOM_CentralUnit2.0_modified.csv, PickAndPlace_CentralUnit2.0.csv]
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2022-01-13 bugfix IMU
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2022-01-14 V2.2 with power line communication
    [BOM_CentralUnit2.0_modified.csv, PickAndPlace_CentralUnit2.0.csv]
2022-01-15 BOM bugfix
    [BOM_PCB_IMU for AgOpenGPS.csv, PickAndPlace_PCB_IMU for AgOpenGPS.csv]
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2022-01-19 two-wire serial option added
    [BOM_CentralUnit3.0_modified.csv, PickAndPlace_CentralUnit3.0.csv]
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2022-01-19 typo correction silkscreen
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2022-01-23 R70, R47, R45 added
    [BOM_CentralUnit2.2.csv, PickAndPlace_CentralUnit2.2.csv]
2022-01-23 discrete torque detection removed
    [BOM_CentralUnit2.2.csv, PickAndPlace_CentralUnit2.2.csv]
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2022-02-12 update to V1.2
    2-wire powerline communikation option added
    [BOM_Section_and_Rate_Control_Unit.csv, Frontpanel_SectionControlUnit_7Sec.dxf, PickAndPlace_SectionControlUnit.csv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]
2022-03-04 bugfix in IMU calculations
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2022-03-19 V2.3: dual-RTK also via two USB
    [BOM_CentralUnit2.2.csv, BOM_CentralUnit2.3.csv, PickAndPlace_CentralUnit2.2.csv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]
2022-03-20 xtra BOM & doc added
    [BOM_CentralUnit2.3.csv, BOM_CentralUnit2.3_(USB-recommended).csv]
2022-03-20 hydraulic pressure sensor enabled
    [BOM_CentralUnit2.3_(USB-recommended).csv]
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

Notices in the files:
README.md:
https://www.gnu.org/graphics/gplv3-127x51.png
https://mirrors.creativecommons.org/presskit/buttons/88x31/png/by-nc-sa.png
